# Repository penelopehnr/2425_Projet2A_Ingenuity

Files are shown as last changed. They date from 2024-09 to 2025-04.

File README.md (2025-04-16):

# 2425_Projet2A_Ingenuity

**Students :**

- Pénélope HENNER - penelope.henner@ensea.fr
- Kavin DUGARD - kevin.dugard@ensea.fr 
- Elio FLANDIN - elio.flandin@ensea.fr
- Joel COLASO - joel.colaso@ensea.fr

## Project background:

Mars 2020 is a space mission to deploy the Perseverance rover on the Martian surface to study its surface and collect soil samples. It is the first of a series of three missions whose ultimate aim is to return these samples to Earth for analysis.

Ingenuity is a small helicopter developed by NASA, the US space agency. It is being used experimentally on the surface of Mars during the Mars 2020 mission. The helicopter is on board the Perseverance rover.

On April 19, 2021, for the first time in the history of the space age, a spacecraft makes a powered flight through the tenuous atmosphere of another planet. Ingenuity's objective is optical reconnaissance of the terrain, with the helicopter taking numerous aerial photos used by the pilots of the Perseverance astromobile to identify obstacles and promising sites (taking rock samples from the Martian soil).

Ingenuity is a 1.8 kg helicopter with 2 coaxial counter-rotating rotors. It draws its energy from 6 lithium-ion batteries recharged by solar cells. Its navigation system enables it to follow a pre-programmed route without human intervention. Its only payload is a camera.

The mission recently came to an end (January 18, 2024) when a blade broke during the 72nd flight.

Ingenuity has opened up new prospects for Mars exploration. NASA and ESA, as part of their Mars sample return mission, are now including 2 similar helicopters to collect the tubes containing the Martian samples deposited by the Perseverance astromobile in the event of its failure.

 Our project is therefore to try to build the Ingenuity module in miniature. In other words, we want to create a vehicle that can move through the air and take a photo of what's going on below.

 [Learn more about the Mars 2020 mission](Ingenuity%20March%202020.md)

Ingenuity picture

## Our project

Our project is to try and make this helicopter in miniature mode. In other words, we want to create a vehicle that can move through the air and take a photo of what's happening below. To do this, we'll have a total of 10 sessions in which we'll have to mix PCBs, coding, soldering and so on.

## Project architecture

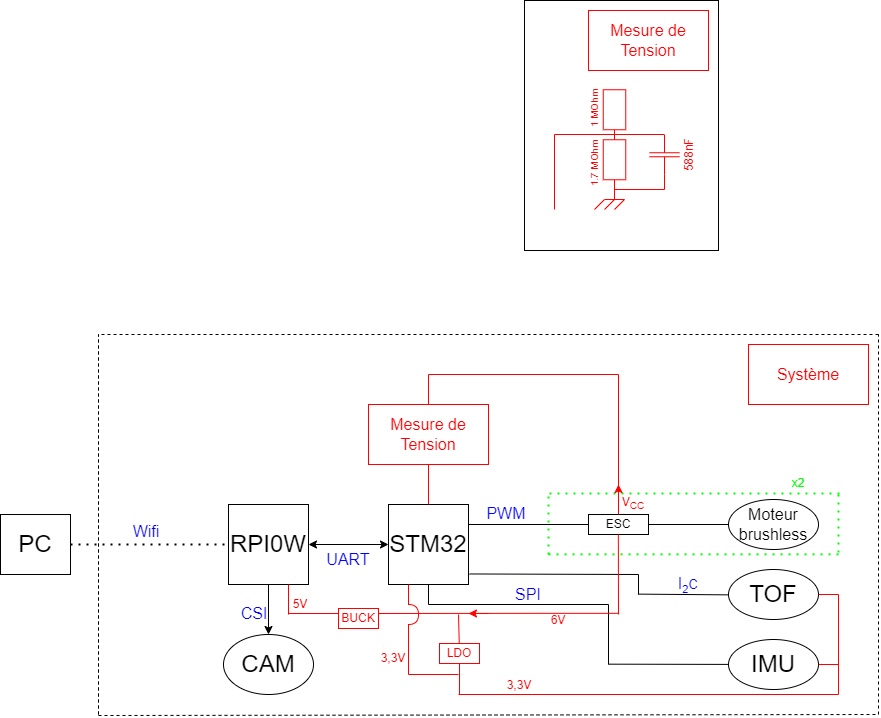
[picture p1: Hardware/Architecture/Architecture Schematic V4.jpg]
Mini Ingenuity Drone architecture


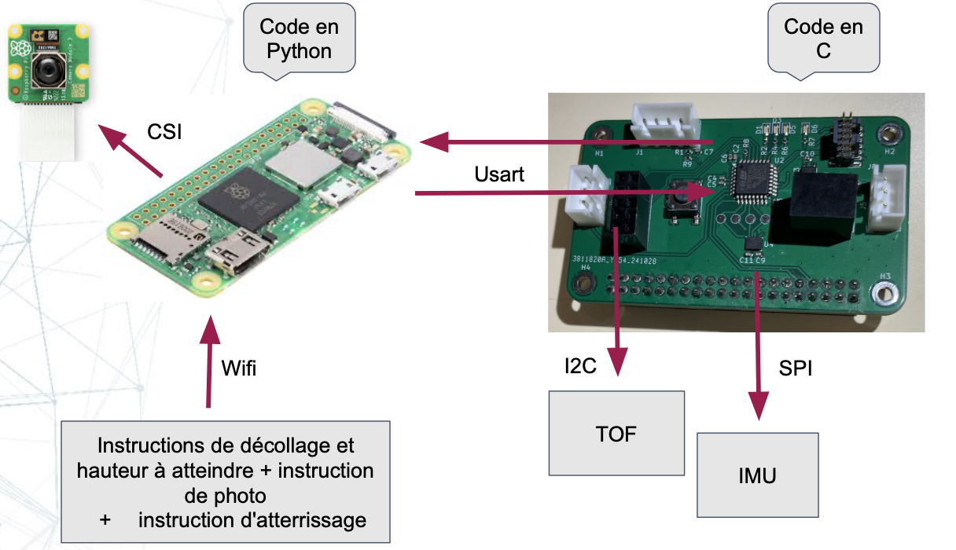
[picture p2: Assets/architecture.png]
Architecture explanations


## Description of repo structure:

``````
.
├── Assets/            # Project images (drone, PCB)
├── Datasheets/        # Component datasheets
├── Hardware/          # Architecture diagrams, KiCad (PCB) files and 3D files
├── Software/          # Embedded code (STM32) + Python code + TOF module
├── README.md          # Main project documentation
├── Ingenuity March 2020.md  # Background on the Mars 2020 mission

``````

In the **Assets** folder, you will find pictures of the drone and the assembled PCB.

The **Datasheets** folder contains documentation for all the components we used throughout the project.

The **Hardware** folder includes all the KiCad files needed to reproduce our custom PCB, along with the Bill of Materials (BOM) listing all components, their references, and specifications. You will also find files for 3D printing and laser cutting the various structural parts of the drone.

The **Software** folder contains:
- The **Python code** used to build the graphical user interface (GUI) on the PC to communicate with the Raspberry Pi (`Client_GUI.py`).
- The **Python code** running on the Raspberry Pi, which handles communication with the microcontroller and takes pictures (`server.py`).
- The **TOF code** (developed with STM32CubeIDE), which is responsible for sending the drone’s altitude using a Time-of-Flight sensor.
- The **C code** (also under STM32CubeIDE) in `Ingenuity_2A`, running on the STM32 microcontroller, which receives commands from the Raspberry Pi and manages the components such as motors, TOF sensor, etc.

## Environments used: 

### Machines Used
- **PC (Windows/macOS/Linux)**: Used for development (STM32CubeIDE, Python, OnShape, etc.).
- **Function Generator (GBF)**: Used to simulate control signals during motor testing.
- **Laser Cutter (FabLab)**: Used to cut the wooden drone structure.

### Hardware
- **Raspberry Pi Zero**: A single-board computer used for image capture, PCB interfacing, and running Python scripts.
- **STM32L412KBT6**: Main microcontroller used on the custom PCB.
- **VL53L1X**: Time-of-Flight (ToF) distance sensor.
- **ESC (Electronic Speed Controllers)**: To control brushless motors.
- **Brushless Motors**: Used to generate drone thrust.
- **LDO BU33TD3WG**: Low-dropout voltage regulator.
- **Buck Converter 17395xx36**: DC-DC converter used to step down voltage.
- **MOSFETs**: Used for power switching and motor control.
- **Camera (connected to Raspberry Pi)**: Captures aerial images.

### Software
#### Embedded Development
- **STM32CubeIDE**: Used to write, compile, and flash firmware to the microcontroller.
- **STM32 HAL Drivers**: Low-level drivers for managing STM32 peripherals.

#### Electronic Design
- **KiCad**: Used for circuit schematic design, PCB layout, and Gerber/BOM export.
- **OnShape**: Used for 3D modeling of the drone structure.

#### Python Development
- **Python 3**: Used for drone communication scripts and the graphical user interface (GUI).
- **Tkinter / PyQt**: Used to build the GUI interface.
- **Pygame / Other sound libraries**: For playing feedback sounds (from the `sounds/` folder).
- **Flask / TCP Sockets**: For communication between the GUI and the drone.

## Precision on the TOF VL53L1X

Start by copying the ```VL53L1X_ULD_API``` in your project. You want to configure the paths in your IDE (eg. in STM32CubeIDE : ```Project > Properties``` then ```C/C++ General > Paths and Symbols```).

Source (code and explanations): https://github.com/lfiack/tof_VL53L1X-SATEL/blob/main/README.md

## Precise notice of our project 

[Mini-Ingenuity notice](Mini-Ingenuity_notice.md)

## Logbook

[Logbook](LogBook.md)

## Picture of Mini-Ingenuity 

Picture of Mini-Ingenuity

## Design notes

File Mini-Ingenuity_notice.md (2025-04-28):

# Utilisation Notice

## General 

The goal of the drone is to take off, reach a predefined altitude, capture a photo, and then descend.

Altitude commands are sent from the PC to the Raspberry Pi Zero via Wi-Fi using Python scripts. A custom graphical interface has been developed on the PC to control this process. The Raspberry Pi then communicates with the microcontroller on the PCB through a UART (USART) serial connection, using both Python and C code. It is also responsible for capturing images through a CSI camera interface.

The microcontroller, embedded on the custom PCB, manages the drone's motors using PWM signals (written in C), and receives altitude data from a Time-of-Flight (TOF) sensor over an I2C bus, also handled via C code.

## Architecture 

Mini Ingenuity Drone architecture

## Structure of Mini-Ingenuity (Hardware files)

### 3D structural parts 
 
files concerned: `Hardware/3D files/files.stl`:
``````
3D files
│   │   ├── 3D_boulons_structure_drone.stl
│   │   ├── 3D_tube_structure_drone.stl
│   │   └── 3D_vises_structure_drone.stl
``````
The screws, bolts, and tubes allow you to assemble the wooden parts together and build the structure of the drone.

Machine used: a 3D printer

3D parts

### Wood structure 

files concerned: `Hardware/Wood structure/Bois.stl`

Our wood sheets are 5 mm thick. 

Machine used: a laser cutter 

### Picture of the Structure 

Picture of the structure

## PCB (Hardware files)

files concerned: `Hardware/KiCAD/...`

### BOM

First, you will need all the required components. You can find all the necessary information — references, quantities, etc. — in the Bill of Materials (BOM).

[BOM](Hardware/KiCAD/BOMv3.csv)

### KiCad

Software used: KiCad
All the KiCad files required to build the PCB are available in this repository.

Picture of the PCB: [PCB Picture](Assets/IMG_6468.png)

## Code (Software)

### Python code 

files concerned: `Software/Python`
requiered functions: `Software/Python/requirements.txt`
Notice : `Software/Python/Notice.md`

#### Initialization

Start by importing all the libraries listed in the `requirements` file. Follow the steps indicated in `Software/Python/Notice.md`.

#### Graphic User Interface

There are a total of five different buttons:  
- First, you must click on the gear icon in the top left corner. This allows you to enter your system's "coordinates": **IP** and **port**.  

- Then, press the button with the Wi-Fi logo on the right to connect to the RPi0 (Note that the script `Software/Python/server.py` must have been executed on the Raspberry Pi beforehand).  

- Now, let's go over the three remaining buttons:  
    - The button on the far left (***Command***) allows you to control the drone's altitude using your keyboard. Here are the available commands:  
        - Alt + UP_Arrow → +1   //   Alt + DOWN_Arrow → -1  
        - UP_Arrow → +5   //   DOWN_Arrow → -5  
        - Ctrl + UP_Arrow → +10   //   Ctrl + DOWN_Arrow → -10  
    - The center button (***Photo***) allows you to take a photo (how to retrieve it is explained in `Notice.md`).  
    - The button on the right (***Auto***) allows you to enter a specific height (in mm) for the drone to reach.

#### Emergency stop

If you want to do an Emergency stop, you just have to tap the ***esc*** touch on your keyboard, this will disconnect the computer to the RPi0 and the speed of the motor will decrease to zero. 

#### Get the photo

To get the photo, everything is explained in the `Software/Python/Notice.md` file. 

### Code for the microcontroller (STM32CubeIDE)

First, if you don't already have it, download the software STM32CubeIDE. 

Use the official ST website: https://www.st.com/en/development-tools/stm32cubeide.html

STM32CubeIDE download capture

Then also download our STM32 project ("Software/C" folder) from this github repository.

You can dowload the repository as shown in the following capture:



Now, you're ready to open the code with STM32CubeIDE. You can click "Open Project from File System..." and select the one you just downloaded.



After that, use the "Project Explorer" view to navigate to the "main.c" file as shown here:



Then plug your STLINK-V3SET cable into the PCB (Green circle in the picture):

STLINK Connected image

Plug the other end to the computer that's running STM32CubeIDE using an USB cable and you are ready to go.

Finally, click the "Run" button to load the program to the microcontroller and start it's execution.

Run program capture

The drone is now ready and will be waiting for the instructions sent by the python powered user interface.

files concerned: `Software/C`

#### PINs

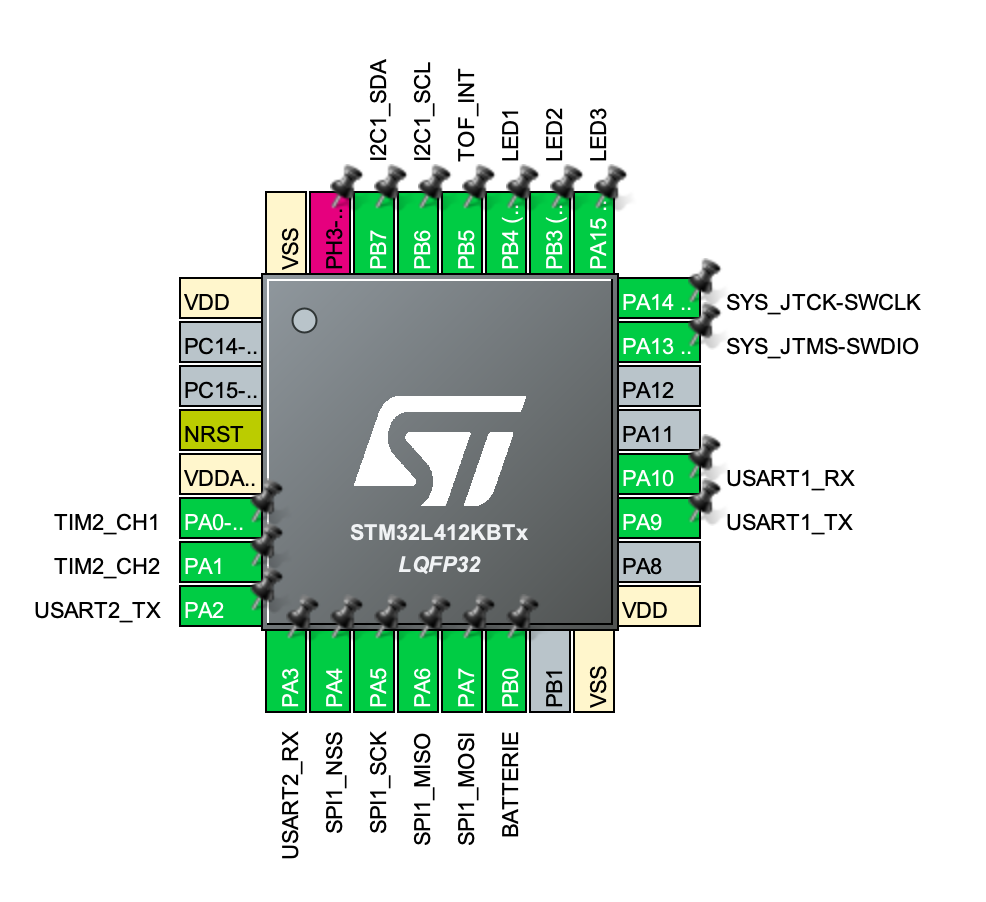
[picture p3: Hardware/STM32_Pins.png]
PIN


### TOF 

Start by copying the ```VL53L1X_ULD_API``` in your project. You want to configure the paths in your IDE (eg. in STM32CubeIDE : ```Project > Properties``` then ```C/C++ General > Paths and Symbols```).

detailed explanations: https://github.com/lfiack/tof_VL53L1X-SATEL/blob/main/README.md

You can refer to the datasheet for information on how to connect to the PCB: 

[TOF Datasheet](Datasheets/TOF.pdf)

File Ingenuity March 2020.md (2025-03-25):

# Ingenuity project 

## Introduction: Ingenuity as part of the Mars 2020 mission. 

Mars 2020 is a space mission that will deploy the Perseverance rover on the Martian surface to study its surface and collect soil samples. It is the first of a series of three missions whose ultimate aim is to return these samples to Earth for analysis. 

Ingenuity is a small helicopter developed by NASA, the US space agency. It is being used experimentally on the surface of Mars during the Mars 2020 mission.
The helicopter is on board the Perseverance rover. 

On April 19, 2021, for the first time in the history of the space age, a spacecraft makes a powered flight through the tenuous atmosphere of another planet. Ingenuity's objective is optical reconnaissance of the terrain, with the helicopter taking numerous aerial photos which are used by the pilots of the Perseverance astromobile to identify obstacles and promising sites (taking rock samples from the Martian soil). The tenuous atmosphere (only 1% of Earth's atmospheric pressure) offers very little lift, making it more difficult to develop an aerobot. 

Ingenuity is a 1.8 kg helicopter with 2 coaxial counter-rotating rotors. It draws its energy from 6 lithium-ion batteries recharged by solar cells. Its navigation system enables it to follow a pre-programmed route without human intervention. Its only payload is a camera. 

The mission recently came to an end (January 18, 2024) when a blade broke during the 72nd flight. 

Ingenuity has opened up new prospects for Mars exploration. NASA and ESA, in their Mars Sample Return mission, are now including 2 similar helicopters which will be responsible for collecting the tubes containing the Mars samples deposited by the Perseverance astromobile in the event of its failure. 

The Mars Sample Return mission will be Ingenuity's first operational use. Developed by NASA in collaboration with the European Space Agency, its aim is to return to Earth the Martian soil samples collected by the Perseverance astromobile. To achieve this objective, the mission plans to send a lander, Sample Retrieval Lander (SRL), carrying a remotely operated arm to retrieve the tubes containing the soil samples. If the soil samples are out of reach of the lander due to a failure of Perseverance, SRL has two Sample Recovery Helicopters, directly derived from the Ingenuity helicopter, equipped with a grabber to retrieve the tubes from where they were deposited.

## First look at the anatomy of the Martian helicopter

NASA's website with extensive information on Ingenuity: (https://mars.nasa.gov/technology/helicopter/#)

## Exploring helicopter operation

### Propulsion: 

The helicopter moves through the air thanks to two coaxial, two-bladed counter-rotating rotors. The rotational speed is between 2,400 and 2,900 rpm, ten times that of a helicopter main rotor on Earth, to be effective in the thin air of Mars. This is a condition we won't be able to meet. 

Understanding how helicopter propellers work helps us to overcome the first difficulties: we need small, coaxial, counter-rotating propellers, parts that we can't build ourselves (3D printing). One solution we've come up with is to use propellers taken from a remote-controlled helicopter. We'll dismantle the aircraft to keep only the propellers on the axis and the engines, and rebuild all the electronics according to our specifications. 

Aircraft type: the use of coaxial counter-rotating rotors saves space compared with the use of an anti-torque rotor. 

### Energy: 

Energy is the main limiting factor concerning the helicopter's capabilities. The energy required for propulsion, sensor operation (altimeter, camera), heating resistors (responsible for maintaining the various systems at a temperature compatible with the operating constraints during the Martian night), avionics, processors and the telecommunications system is supplied by six lithium-ion accumulators, with a capacity of 36 Watts-h recharged by photovoltaic cells (active surface area of 544 cm^2).

### Sensors: 

- a navigation camera
- 2 3-axis inertial units (acceleration and rotation speed)
- 2-axis inclinometer
- altimeter

### Telecommunications: 

Given the time taken for Mars-to-Earth communication (around ten minutes in favorable conditions), the helicopter flies autonomously, applying instructions transmitted beforehand. In flight, the helicopter does not receive, but transmits the data it has collected. 

### Avionics and processors:

The avionics are distributed over 5 circuit boards, 4 of which form the sides of the cubic fuselage and the fifth the inside. The on-board computer uses a Snapdragon microprocessor clocked at 2.26 GHz, with 2 GB RAM and 32 GB flash memory. The computer supports the navigation function and controls the rotors via two redundant microcontrollers. The software running on the microprocessor is supported by an FPGA-type integrated circuit, which handles functions such as altitiude control, I/O management of the inertial unit, altimeter and inclinometer, and telecommunications management. The FPGA is a militarized version of MicroSemi's ProASIC3L. The operating system is GNU/Linux. 

### Sources: 

https://mars.nasa.gov/technology/helicopter/#Tech-Specs

https://fr.wikipedia.org/wiki/Ingenuity_(hélicoptère)

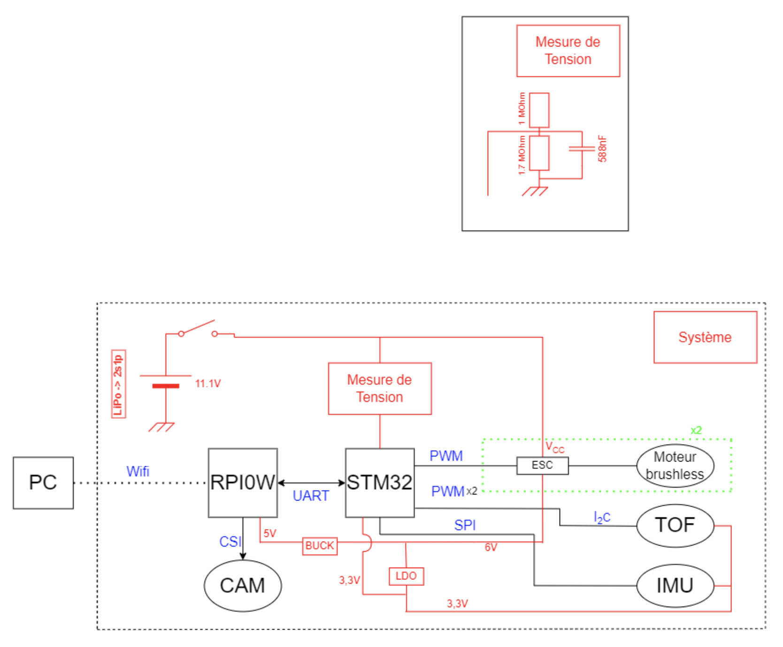
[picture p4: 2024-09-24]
Hardware/Architecture/Architecture Schematic V2.jpg

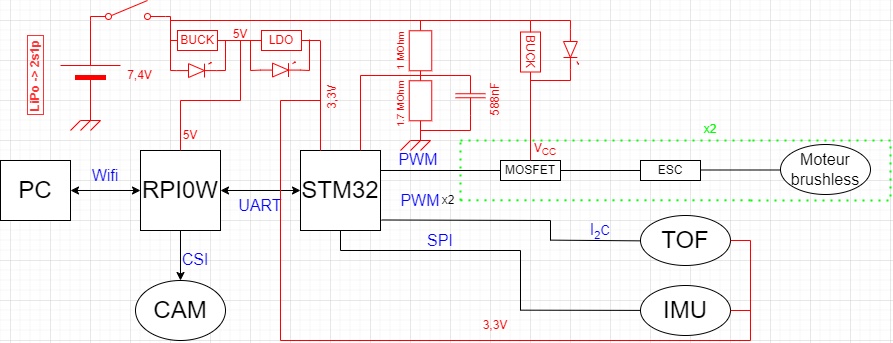
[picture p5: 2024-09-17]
Hardware/Architecture/Architecture Schematic V1.jpg

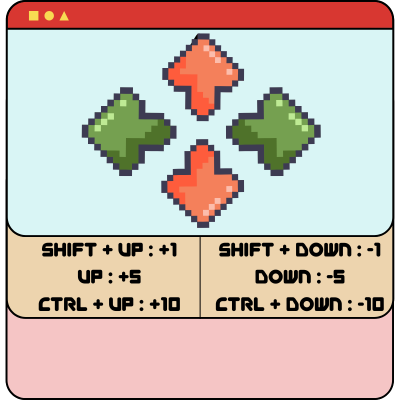
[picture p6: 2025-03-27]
Software/Python/img/Command.png

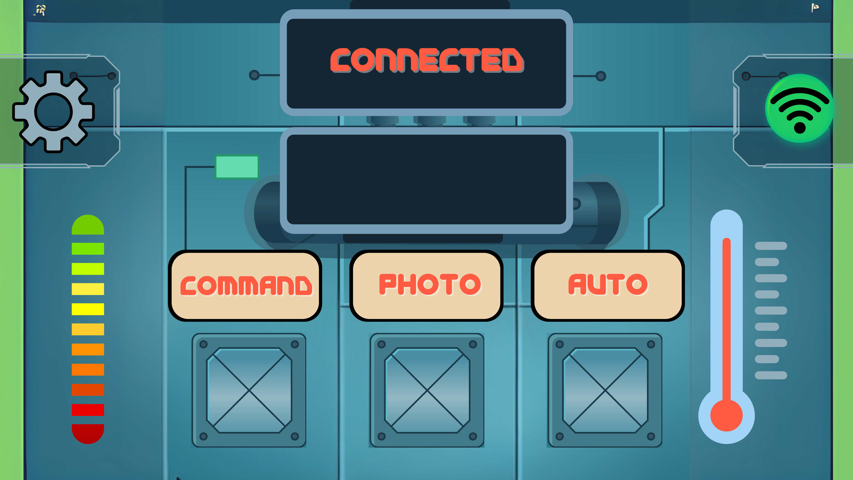
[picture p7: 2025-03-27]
Software/Python/img/Connected.png

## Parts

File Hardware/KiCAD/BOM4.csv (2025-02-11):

Reference | Value | Datasheet | Footprint | Qty | DNP | MPN
C1 | 10u | ~ | Capacitor_SMD:C_0603_1608Metric | 1
C2,C3,C4,C5,C7,C9,C11 | 100n | ~ | Capacitor_SMD:C_0402_1005Metric | 7
C6 | 4u7 | ~ | Capacitor_SMD:C_0402_1005Metric | 1
C8,C10 | 1u | ~ | Capacitor_SMD:C_0402_1005Metric | 2
D1,D3,D5,D6 | LED | ~ | LED_SMD:LED_0603_1608Metric | 4
H1,H2,H3,H4 | MountingHole_Pad | ~ | MountingHole:MountingHole_2.7mm_M2.5_DIN965_Pad | 4
J1 | Conn_01x04 | ~ | Connector_JST:JST_XH_B4B-XH-A_1x04_P2.50mm_Vertical | 1
J2,J6 | Conn_02x05_Odd_Even | ~ | Connector_PinHeader_2.54mm:PinHeader_2x05_P2.54mm_Vertical | 2
J4,J5 | Conn_01x03 | ~ | Connector_JST:JST_XH_B3B-XH-A_1x03_P2.50mm_Vertical | 2
J8 | Conn_ST_STDC14 | https://www.st.com/content/ccc/resource/technical/document/user_manual/group1/99/49/91/b6/b2/3a/46/e5/DM00526767/files/DM00526767.pdf/jcr:content/translations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 | Connector_PinHeader_1.27mm:PinHeader_2x07_P1.27mm_Vertical_SMD | 1
R1 | 27k | ~ | Resistor_SMD:R_0402_1005Metric | 1
R2,R4,R6,R7 | 165 | ~ | Resistor_SMD:R_0402_1005Metric | 4
R8,R9 | 10k | ~ | Resistor_SMD:R_0402_1005Metric | 2
SW2 | SW_Push | ~ | Button_Switch_SMD:SW_Push_1P1T_NO_6x6mm_H9.5mm | 1
TP1 | TestPoint | ~ | TestPoint:TestPoint_Pad_D1.5mm | 1 | DNP
TP2,TP3,TP4,TP5,TP6 | TestPoint | ~ | TestPoint:TestPoint_Pad_D1.5mm | 5
U1 | ~ |  | myemp:Buck_ing | 1 |  | 173950536
U2 | STM32L412KBTx | https://www.st.com/resource/en/datasheet/stm32l412kb.pdf | Package_QFP:LQFP-32_7x7mm_P0.8mm | 1 |  | STM32L412KBT6
U3 | BU33TD3WG | https://ww1.microchip.com/downloads/aemDocuments/documents/OTH/ProductDocuments/DataSheets/MIC5317-High-Performance-Single-150mA-LDO-DS20006195B.pdf | Package_TO_SOT_SMD:SOT-23-5 | 1 |  | BU33TD3WG-TR
U4 | LSM6DSM | https://www.st.com/resource/en/datasheet/lsm6dsm.pdf | Package_LGA:LGA-14_3x2.5mm_P0.5mm_LayoutBorder3x4y | 1 |  | LSM6DSMTR

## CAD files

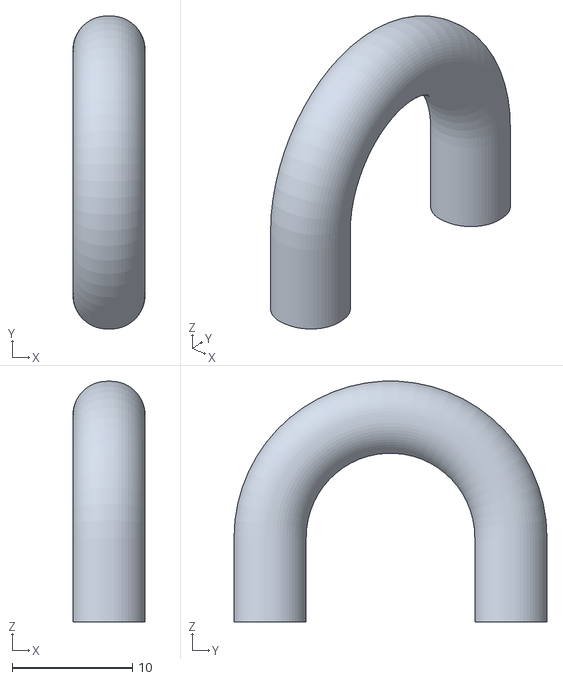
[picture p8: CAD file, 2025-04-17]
Hardware/3D files/3D_handle_structure_drone.stl
6.00 x 26.0 x 20.0

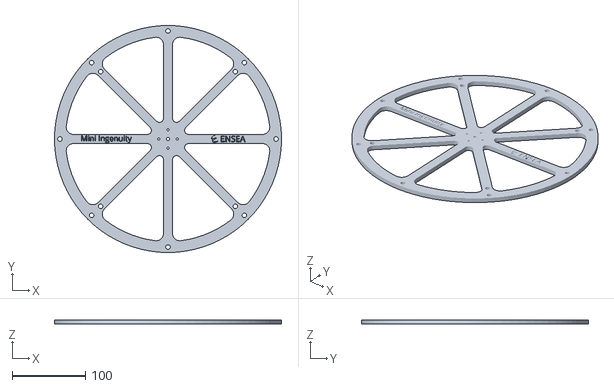
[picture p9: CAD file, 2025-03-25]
Hardware/Wood structure/Wooden_structure.stl
310.0 x 310.0 x 6.00

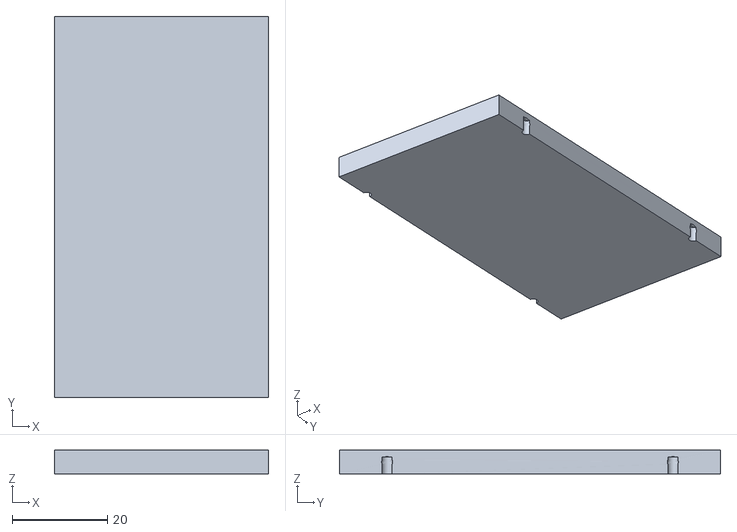
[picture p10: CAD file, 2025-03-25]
Hardware/3D files/3D_hatch_structure_drone.stl
45.0 x 80.0 x 5.00

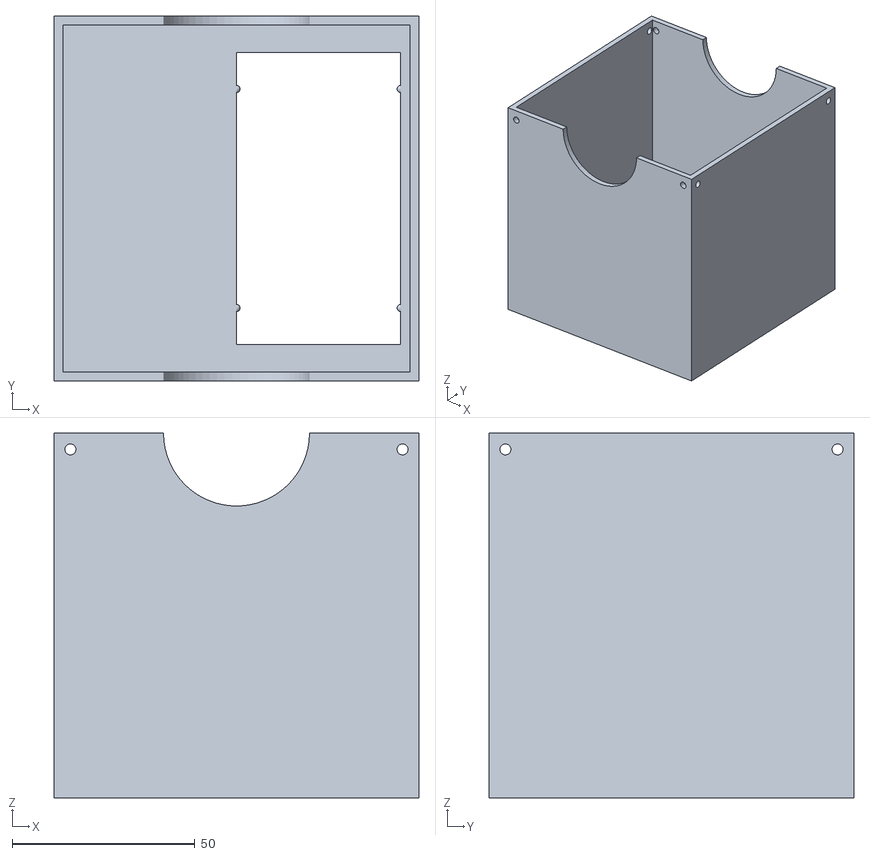
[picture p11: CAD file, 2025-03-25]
Hardware/3D files/3D_box_electronics_structure_drone.stl
100.0 x 100.0 x 100.0

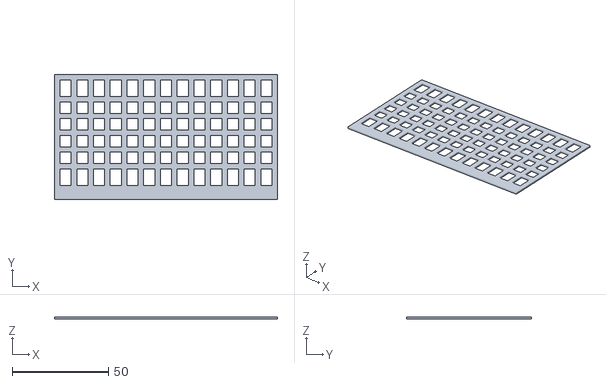
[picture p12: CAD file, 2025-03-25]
Hardware/3D files/3D_protection_structure_drone.stl
116.0 x 65.0 x 1.00

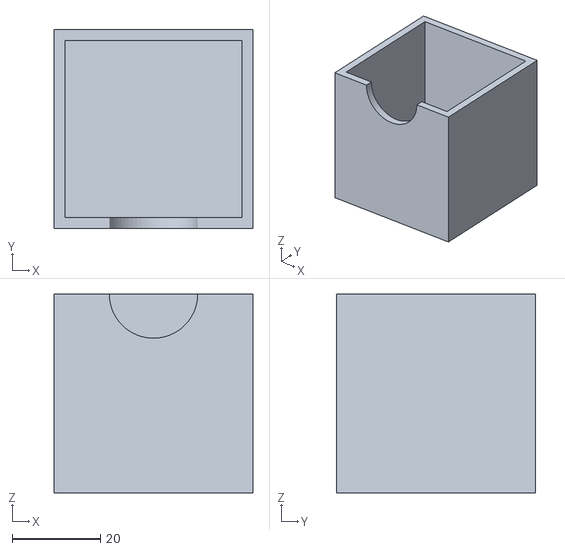
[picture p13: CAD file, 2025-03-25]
Hardware/3D files/3D_box_motor_structure_drone.stl
45.0 x 45.0 x 45.0

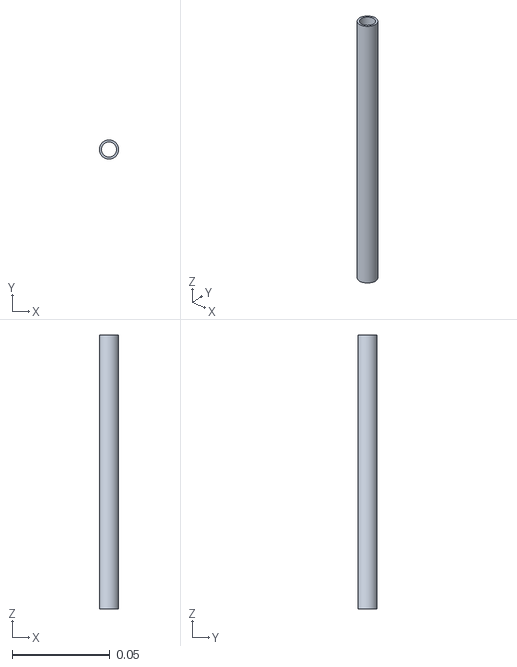
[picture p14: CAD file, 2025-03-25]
Hardware/3D files/3D_tube_structure_drone.stl
0.0098 x 0.0098 x 0.14

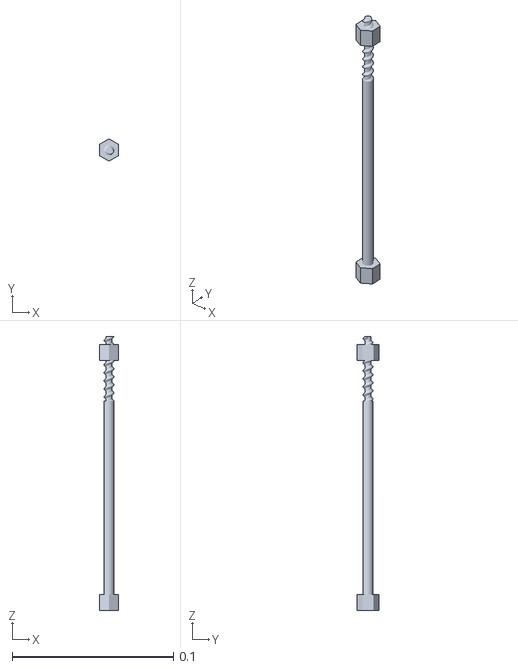
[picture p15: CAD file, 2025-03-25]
Hardware/3D files/3D_screw_structure_drone.stl
0.012 x 0.0139 x 0.17

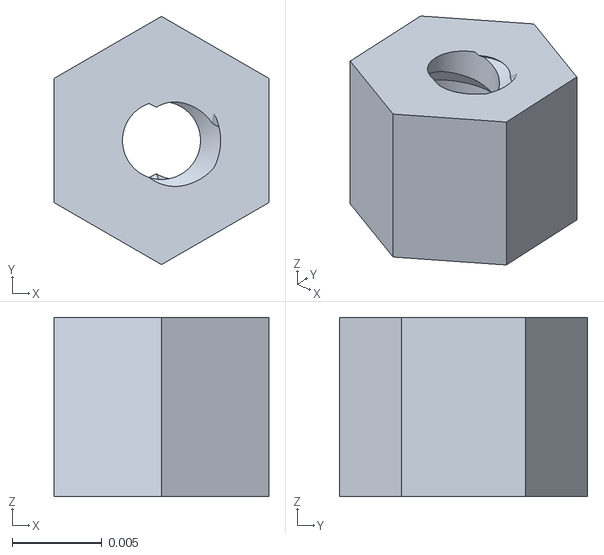
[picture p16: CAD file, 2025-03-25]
Hardware/3D files/3D_bolts_structure_drone.stl
0.012 x 0.0139 x 0.01

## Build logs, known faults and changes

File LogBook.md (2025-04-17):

## Project Logbook – Ingenuity

### Table of Contents
- [Session 1 (08/10/2024)](#session-1-08102024)
- [Session 2 (22/10/2024)](#session-2-22102024)
- [Session 3 (05/11/2024)](#session-3-05112024)
- [Session 4 (12/11/2024)](#session-4-12112024)
- [Session 5 (19/11/2024)](#session-5-19112024)
- [Session 6 (26/11/2024)](#session-6-26112024)
- [Session 7 (03/12/2024)](#session-7-03122024)
- [Session 8 (10/12/2024)](#session-8-10122024)
- [Session 9 (14/12/2024)](#session-9-14122024)
- [Session 10 (21/12/2024)](#session-10-21122024)
- [Session 11 (28/12/2024)](#session-11-28122024)
- [Session 12 (28/01/2025)](#session-12-28012025)
- [Session 13 (04/02/2025)](#session-13-04022025)
- [Session 14 (11/02/2025)](#session-14-11022025)
- [Session 15 (04/03/2025)](#session-15-04032025)
- [Session 16 (11/03/2025)](#session-16-11032025)
- [Session 17 (18/03/2025)](#session-17-18032025)
- [Session 18 (25/03/2025)](#session-18-25032025)
- [Session 19 (01/04/2025)](#session-19-01042025)

### Session 1 (08/10/2024)
- Modeled the initial architecture diagram (V1).
- Started writing the project structure.
- Researched higher-performing components compared to last year (Buck, LDO, motors, etc.).
- Added datasheets for the final selected components.

### Session 2 (22/10/2024)
- Reflected on the architecture and created versions V2 and V3.
- Added new component datasheets.

### Session 3 (05/11/2024)
- Uploaded the final datasheets to Git.
- Finalized architecture diagram (V4).
- Started schematic modeling in KiCad.
- Began C programming on the STM32.
- Started the Python code base.

### Session 4 (12/11/2024)
- Updated the Python code.
- Created documentation for the Python scripts.
- Continued PCB routing in KiCad.

### Session 5 (19/11/2024)
- Exported the Bill of Materials (BOM).
- Soldered the PCB at school.
- Completed PCB soldering between sessions 5 and 6.
- Translated the GitHub repository content into English.

### Session 6 (26/11/2024)
- Tested PCB functionality (LEDs lit up correctly).
- Updated and extended Python code.
- Desoldered the Buck converter due to incorrect output voltage (3V instead of 5V).
- Soldered a new Buck converter and updated the BOM.

### Session 7 (03/12/2024)
- Soldered a Y-cable to connect both ESC drivers simultaneously.
- Tested the drone using a Function Generator (GBF) only.
- Conducted a flight test using the functional PCB and GBF instead of a battery.
- Began 3D modeling the drone structure on OnShape.
- Continued development in both Python and C.

### Session 8 (10/12/2024)
- Visited the FabLab in Cergy to use the laser cutter for wooden drone parts.

### Session 9 (14/12/2024)
- Assembled the drone structure.
- Performed additional flight tests with the assembled drone, GBF, and PCB.
- Finalized the GitHub translation.
- Conducted multiple tests with the Raspberry Pi camera.

### Session 10 (21/12/2024)
- Fully revised and translated the README.
- Started development of a Python graphical interface.
- Soldered a JFT-to-banana cable to power the Raspberry Pi more efficiently and continued testing.

### Session 11 (28/12/2024)
- Finalized the Python GUI base.
- Modified KiCad due to a connection issue between the Raspberry Pi Zero and the PCB (reversed connector) → adjusted routing accordingly.
- Started development of TOF (Time-of-Flight) sensor code in C.

### Session 12 (28/01/2025)
- Final adjustments in KiCad: resized PCB to match the Raspberry Pi Zero form factor, completed routing, and prepared for manufacturing.
- Continued TOF sensor code development.

### Session 13 (04/02/2025)
- Drone testing: validated communication and functionality between the PCB, Raspberry Pi Zero, and ESCs using GBF signals. Fixed bugs.
- Improved motor control code in C: enabled gradual speed increases and added keyboard controls.
- Continued TOF code development.

### Session 14 (11/02/2025)
- Soldered the new version of the PCB.
- Tested communication with the Raspberry Pi Zero and improved the C code (added linear acceleration for motors).
- Enhanced the Python GUI: enabled full drone control (connection, camera, power).
- Considered the drone’s weight and explored optimization options.

### Session 15 (04/03/2025)
- Tested the new PCB: power supply and components functioned correctly.
- Added new features to the Python GUI.
- Continued development of C code (motor control + TOF data handling).

### Session 16 (11/03/2025)
- Finalized the TOF code and started IMU integration (C language).
- 3D modeling: designed motor protection casings and an enclosure for electronics.
- Created custom 3D screws and bolts to reduce weight vs traditional threaded rods.
- 3D printed all new parts.

### Session 17 (18/03/2025)
- Full drone test with TOF, IMU, and integrated C code for autonomous flight via GUI.
- Structural optimization: reduced wood frame thickness to cut weight.
- 3D printed updated structural parts.

### Session 18 (25/03/2025)
- 3D modeling: designed propeller protection grilles.
- 3D printed the new protective elements.
- Improved GitHub repository: reorganized and refined the ReadMe.

### Session 19 (01/04/2025)
- Finalized the GitHub repository: added pictures and reorganized the ReadMe and general documentation.
- Assembled the drone: mounted all electronic components onto the 3D-printed frame.
- Gave a flight demonstration of our drone in front of the professors.

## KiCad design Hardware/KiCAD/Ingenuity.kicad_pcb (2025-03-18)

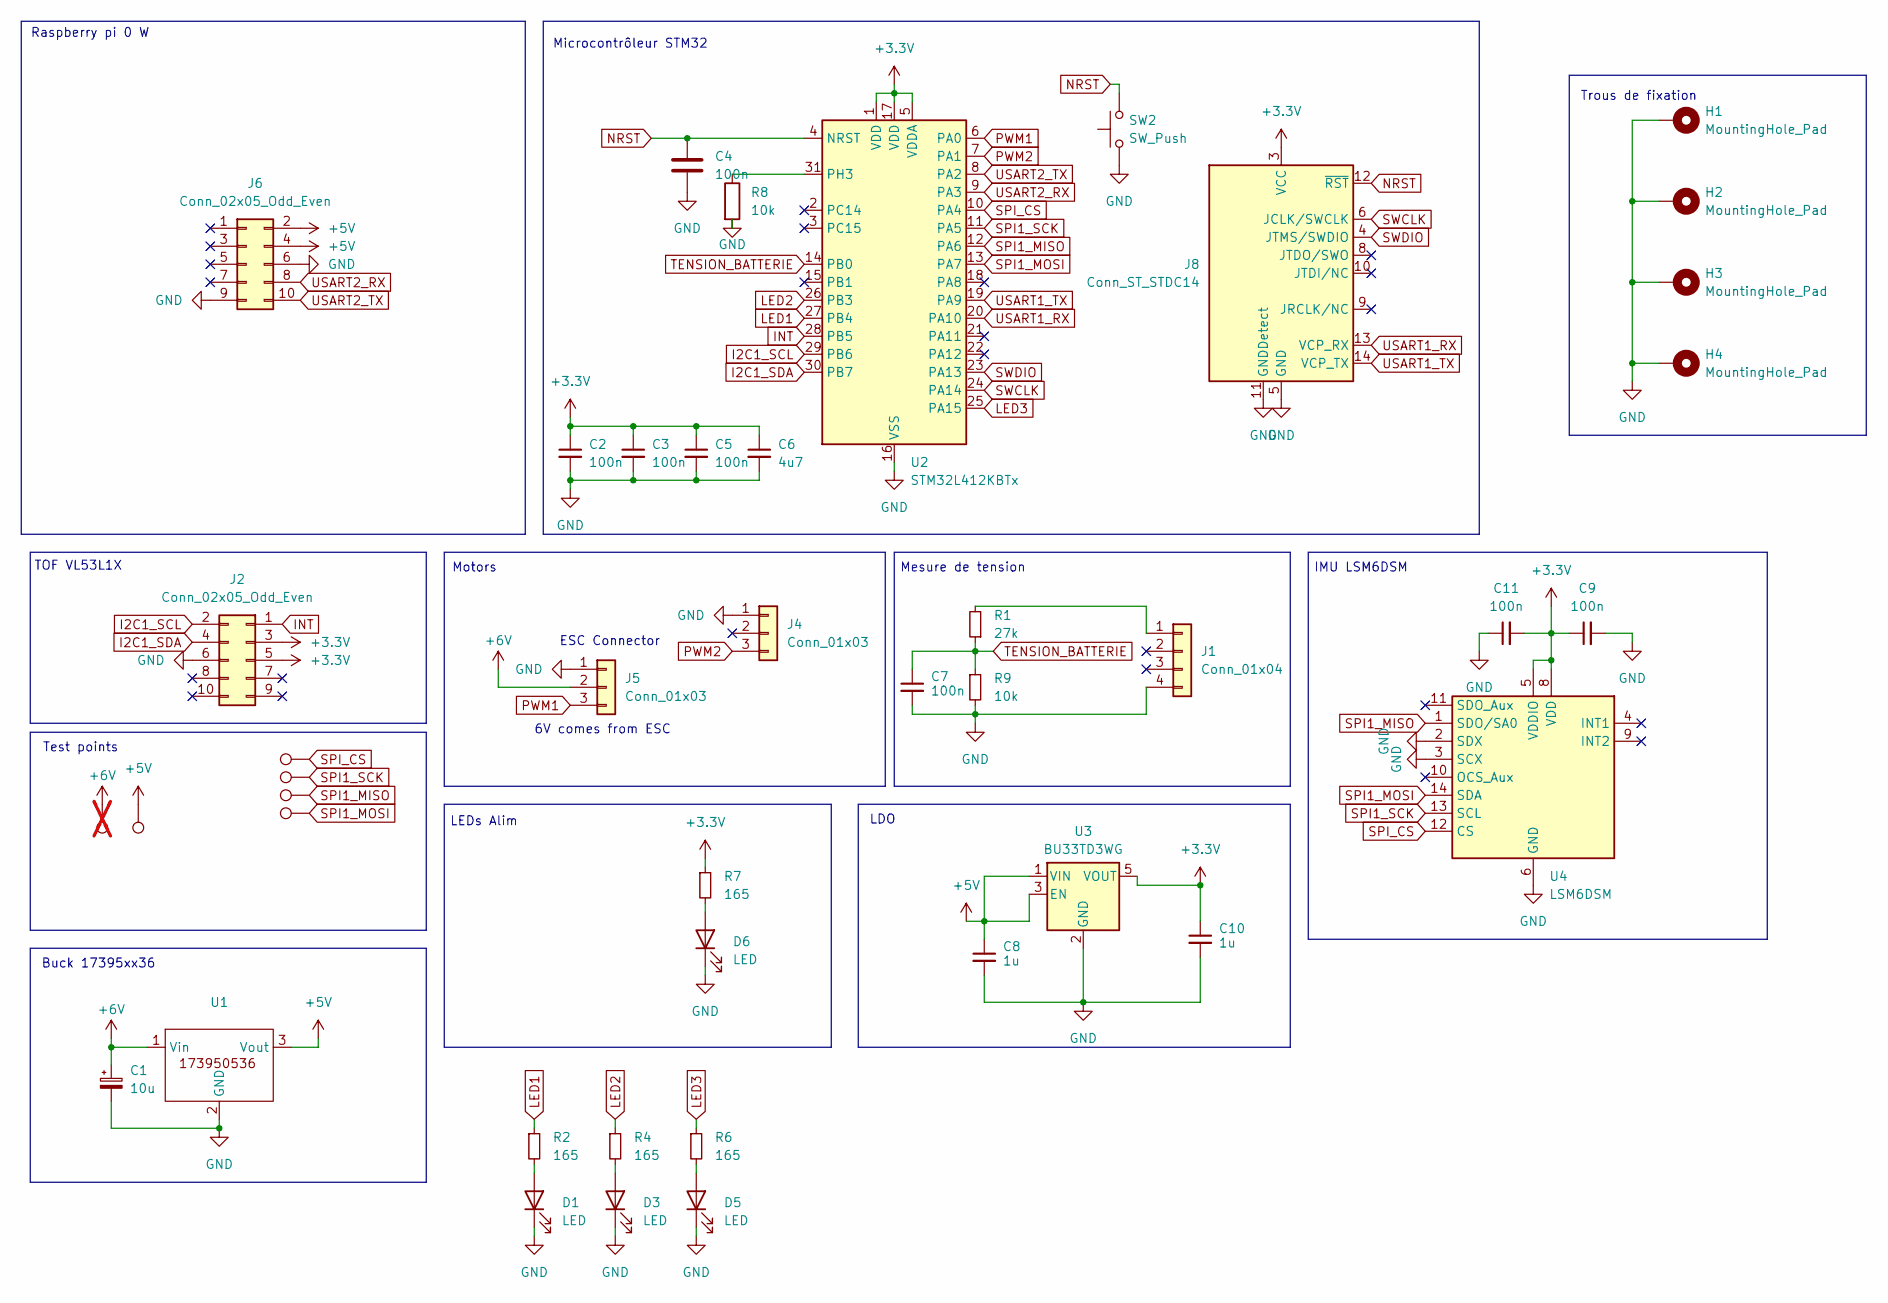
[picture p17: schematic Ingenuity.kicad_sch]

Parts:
C1: 10u; C_0603_1608Metric
C2, C3, C4, C5, C7, C9, C11: 100n; C_0402_1005Metric
C6: 4u7; C_0402_1005Metric
C8, C10: 1u; C_0402_1005Metric
D1, D3, D5, D6: LED; LED_0603_1608Metric
H1, H2, H3, H4: MountingHole_Pad; MountingHole_2.7mm_M2.5_DIN965_Pad
J1: Conn_01x04; JST_XH_B4B-XH-A_1x04_P2.50mm_Vertical
J2, J6: Conn_02x05_Odd_Even; PinHeader_2x05_P2.54mm_Vertical
J4, J5: Conn_01x03; JST_XH_B3B-XH-A_1x03_P2.50mm_Vertical
J8: Conn_ST_STDC14; PinHeader_2x07_P1.27mm_Vertical_SMD
R1: 27k; R_0402_1005Metric
R2, R4, R6, R7: 165; R_0402_1005Metric
R8, R9: 10k; R_0402_1005Metric
SW2: SW_Push; SW_Push_1P1T_NO_6x6mm_H9.5mm
TP1: TestPoint; TestPoint_Pad_D1.5mm; not fitted
TP2, TP3, TP4, TP5, TP6: TestPoint; TestPoint_Pad_D1.5mm
U1: Buck_ing; MPN 173950536
U2: STM32L412KBTx; LQFP-32_7x7mm_P0.8mm; MPN STM32L412KBT6
U3: BU33TD3WG; SOT-23-5; MPN BU33TD3WG-TR
U4: LSM6DSM; LGA-14_3x2.5mm_P0.5mm_LayoutBorder3x4y; MPN LSM6DSMTR

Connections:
+3.3V: C2.1, C3.1, C5.1, C6.1, C9.1, C10.1, C11.2, J2.3, J2.5, J8.3 (VCC), R7.1, U2.1 (VDD), U2.5 (VDDA), U2.17 (VDD), U3.5 (VOUT), U4.5 (VDDIO), U4.8 (VDD)
+5V: C8.1, J6.1, J6.2, J6.4, TP2.1, U1.3 (Vout), U3.1 (VIN), U3.3 (EN)
+6V: C1.1, J5.2, TP1.1, U1.1 (Vin)
GND: C1.2, C2.2, C3.2, C4.2, C5.2, C6.2, C7.2, C8.2, C9.2, C10.2, C11.1, D1.1 (K), D3.1 (K), D5.1 (K), D6.1 (K), H1.1, H2.1, H3.1, H4.1, J1.4, J2.6, J4.1, J5.1, J6.6, J6.9, J8.5 (GND), J8.7 (GND), J8.11 (GNDDetect), R8.2, R9.2, SW2.1, U1.2 (GND), U2.16 (VSS), U2.32 (VSS), U3.2 (GND), U4.2 (SDX), U4.3 (SCX), U4.6 (GND), U4.7 (GND)
I2C1_SCL: J2.2, U2.29 (PB6)
I2C1_SDA: J2.4, U2.30 (PB7)
INT: J2.1, U2.28 (PB5)
LED1: R2.1, U2.27 (PB4)
LED2: R4.1, U2.26 (PB3)
LED3: R6.1, U2.25 (PA15)
NRST: C4.1, J8.12 (~RST), SW2.2, U2.4 (NRST)
unnamed: D1.2 (A), R2.2
unnamed: D3.2 (A), R4.2
unnamed: D5.2 (A), R6.2
unnamed: D6.2 (A), R7.2
unnamed: J1.1, R1.2
unnamed: R8.1, U2.31 (PH3)
PWM1: J5.3, U2.6 (PA0)
PWM2: J4.3, U2.7 (PA1)
SPI1_MISO: TP5.1, U2.12 (PA6), U4.1 (SDO/SA0)
SPI1_MOSI: TP6.1, U2.13 (PA7), U4.14 (SDA)
SPI1_SCK: TP4.1, U2.11 (PA5), U4.13 (SCL)
SPI_CS: TP3.1, U2.10 (PA4), U4.12 (CS)
SWCLK: J8.6 (JCLK/SWCLK), U2.24 (PA14)
SWDIO: J8.4 (JTMS/SWDIO), U2.23 (PA13)
TENSION_BATTERIE: C7.1, R1.1, R9.1, U2.14 (PB0)
USART1_RX: J8.13 (VCP_RX), U2.20 (PA10)
USART1_TX: J8.14 (VCP_TX), U2.19 (PA9)
USART2_RX: J6.8, U2.9 (PA3)
USART2_TX: J6.10, U2.8 (PA2)

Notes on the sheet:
Trous de fixation
Mesure de tension
Motors
LDO
6V comes from ESC
Buck 17395xx36
Raspberry pi 0 W
IMU LSM6DSM
Test points
ESC Connector
LEDs Alim
Microcontrôleur STM32
TOF VL53L1X

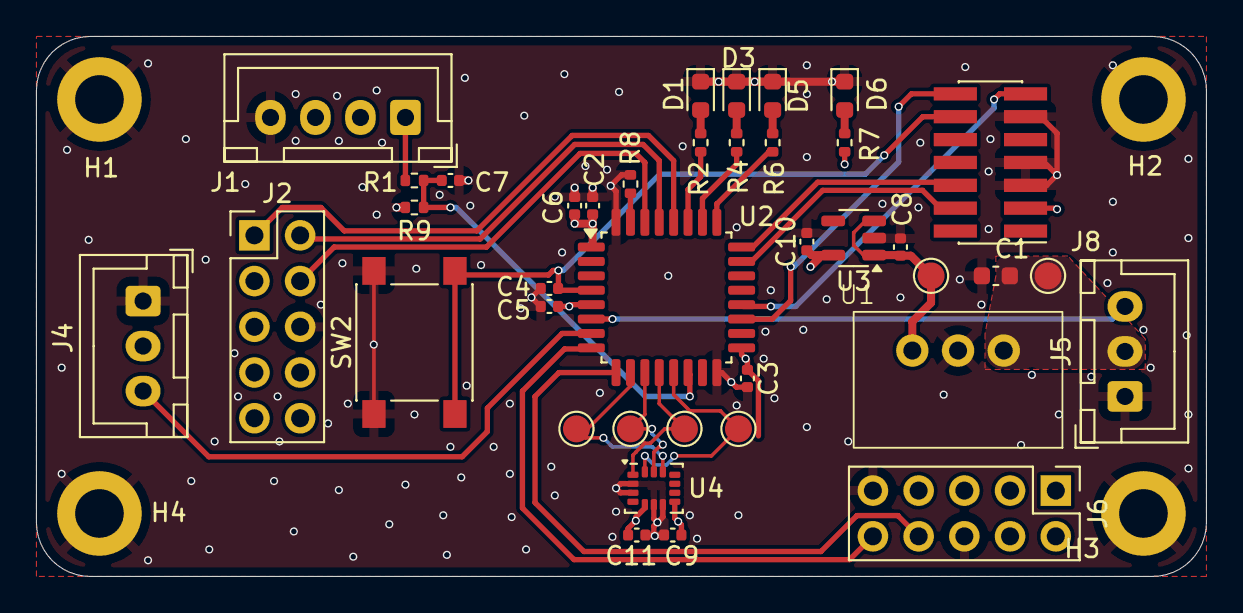
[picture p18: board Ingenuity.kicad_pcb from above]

Board: 4 copper layers, 65.0 x 30.0 mm, 43 parts (0 on the bottom side), 30 nets.

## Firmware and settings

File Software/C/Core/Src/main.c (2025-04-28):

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
/* Includes ------------------------------------------------------------------*/
#include "main.h"
#include "adc.h"
#include "i2c.h"
#include "spi.h"
#include "tim.h"
#include "usart.h"
#include "gpio.h"

/* USER CODE BEGIN Includes */
#include "string.h"
#include "motor.h"
#include "decodeInstruction.h"
#include "stdio.h"
#include "stdlib.h"
#include "math.h"

//////////////////////////////////////////////////////////////////////////////////////////////////////////////////
#include "VL53L1X_api.h"
#include "vl53l1_error_codes.h"


/* USER CODE END Includes */

/* USER CODE BEGIN PD */
#define MAX_ACK_MESSAGE_LENGTH 256

/////////////////////////////////////////////////////////////////////////////////////////////////////////////////
#define VL53L1X_DEFAULT_ADDRESS (0x29 << 1)

/* USER CODE END PD */


void SystemClock_Config(void);
/* USER CODE BEGIN 0 */
int __io_putchar(int ch)
{
  HAL_UART_Transmit(&huart1, (uint8_t *)&ch, 1, HAL_MAX_DELAY);
  return ch;
}

int __io_getchar(void)
{
  uint8_t ch = 0;
  __HAL_UART_CLEAR_OREFLAG(&huart1);
  HAL_UART_Receive(&huart1, (uint8_t *)&ch, 1, HAL_MAX_DELAY);
  HAL_UART_Transmit(&huart1, (uint8_t *)&ch, 1, HAL_MAX_DELAY);
  return ch;
}


char startChar = '@';
char endChar = '#';

uint8_t rx_char; // Variable to store the received character

char instruction[200];
int indexInstruction = 0;

int UARTReceiverState = 0;

volatile int flagUART1 = 0;
volatile int flagTIM6 = 0;


void HAL_TIM_PeriodElapsedCallback(TIM_HandleTypeDef * htim) {
	if (htim -> Instance == TIM6) {
		flagTIM6 = 1;
	}
}


void HAL_UART_RxCpltCallback(UART_HandleTypeDef *huart) {

	instruction[indexInstruction] = rx_char;
	indexInstruction++;

	// Re-enable UART interrupt reception
	HAL_UART_Receive_IT(&huart2, &rx_char, 1);

	if (rx_char == '#')
	{
		instruction[indexInstruction] = 0; // 0 character for the printf
		indexInstruction = 0;
		flagUART1 = 1;
	}
}


uint32_t measure_counter = 0;
uint8_t data_available = 0;
uint16_t distance;

void HAL_GPIO_EXTI_Callback(uint16_t GPIO_Pin)
{
	if (TOF_INT_Pin == GPIO_Pin)
	{
		measure_counter++;
		data_available++;
	}
}


/* USER CODE END 0 */

/**
  * @brief  The application entry point.
  * @retval int
  */
int main(void)
{

  /* MCU Configuration--------------------------------------------------------*/

  /* Reset of all peripherals, Initializes the Flash interface and the Systick. */
  HAL_Init();

  /* Configure the system clock */
  SystemClock_Config();

  /* Initialize all configured peripherals */
  MX_GPIO_Init();
  MX_ADC1_Init();
  MX_I2C1_Init();
  MX_SPI1_Init();
  MX_TIM2_Init();
  MX_USART1_UART_Init();
  MX_USART2_UART_Init();
  MX_TIM6_Init();
  /* USER CODE BEGIN 2 */

  //////////////////////////////////////////////////////////////////////////////////////////////////////////////////////////////////
	printf("\r\n===== VL53L1X-SATEL =====\r\n");

	uint16_t id;
	if (VL53L1X_GetSensorId(VL53L1X_DEFAULT_ADDRESS, &id) != VL53L1_ERROR_NONE)
	{
		Error_Handler();
	}
	printf("SensorID : 0x%X\r\n", id);

	VL53L1X_Version_t version;
	if (VL53L1X_GetSWVersion(&version) != VL53L1_ERROR_NONE)
	{
		Error_Handler();
	}
	printf("Version : %u.%ub%ur%lu\r\n", version.major, version.minor, version.build, version.revision);

	uint8_t boot_state = 0;
	uint8_t boot_state_counter = 0;

	while(boot_state == 0)
	{
		boot_state_counter++;
		if (VL53L1X_BootState(VL53L1X_DEFAULT_ADDRESS, &boot_state) != VL53L1_ERROR_NONE)
		{
			Error_Handler();
		}
		HAL_Delay(1);
	}

	printf("Chip booted in %d...\r\n", boot_state_counter);

	//Loads the 135 bytes default values to initialize the sensor.
	if (VL53L1X_SensorInit(VL53L1X_DEFAULT_ADDRESS) != VL53L1_ERROR_NONE)
	{
		Error_Handler();
	}
	printf("Sensor initialized with the default values\r\n");

	if (VL53L1X_SetDistanceMode(VL53L1X_DEFAULT_ADDRESS, 1) != VL53L1_ERROR_NONE) // 1=short, limited to 1.3m
	{
		Error_Handler();
	}
	printf("Short distance mode\r\n");

	if (VL53L1X_SetTimingBudgetInMs(VL53L1X_DEFAULT_ADDRESS, 50) != VL53L1_ERROR_NONE) // in ms possible values [20, 50, 100, 200, 500]
	{
		Error_Handler();
	}

	if (VL53L1X_SetInterMeasurementInMs(VL53L1X_DEFAULT_ADDRESS, 50) != VL53L1_ERROR_NONE) // in ms, IM must be >= TB
	{
		Error_Handler();
	}

	printf("Timing budget set\r\n");

	if (VL53L1X_StartRanging(VL53L1X_DEFAULT_ADDRESS) != VL53L1_ERROR_NONE)
	{
		Error_Handler();
	}

	  ///////////////////////////////////////////////////////////////////////////////////////////////////////////////////////////////////





  //Start Timer 6
  HAL_TIM_Base_Start_IT(&htim6);

	printf("--------------EXECUTION BEGINS--------------\r\n\n");

	// We define the dictionary of variables that can get modified by receiving a UART signal
	float height = 0.0;
	float LEDState = 0.0;
	float eLanding = 0.0;
	char* variableNames[3] = {"height", "LEDState", "eLanding"};
	float* variablePointers[3] = {&height, &LEDState, &eLanding};
	DictOfFloatVariables dictOfVariables = {
		.n = 3,
		.variableNames = variableNames,
		.variables = variablePointers
	};


	h_motor_t upperMotor;
	h_motor_t lowerMotor;

	upperMotor.htim = &htim2;
	lowerMotor.htim = &htim2;

	upperMotor.channel = TIM_CHANNEL_1;
	lowerMotor.channel = TIM_CHANNEL_2;

	MOTOR_InitBoth(&lowerMotor, &upperMotor);


	// Important, initiate character reception.
	// This line also being in HAL_UART_RxCpltCallback's body ensures continuous reception
	HAL_UART_Receive_IT(&huart2, &rx_char, 1);



  /* USER CODE END 2 */

  /* Infinite loop */
  /* USER CODE BEGIN WHILE */

  // This variable sets if the vertical control is constant (0), proportional (1) or proportional-derivative (2)
  int approach = 1;

  // Variables for Proportional Derivative Approach
  float Kp = 1.0;
  float Kd = 0.5;

  float previousError = 0;
  float dt = 0.05; // Time step (I calculated it based on our tim6 configuration)

  while (1)
  {

	  if (data_available > 0)
		{
			data_available = 0;
			uint16_t newDistance;

			if (VL53L1X_ClearInterrupt(VL53L1X_DEFAULT_ADDRESS) != VL53L1_ERROR_NONE)
			{
				Error_Handler();
			}
			if (VL53L1X_GetDistance(VL53L1X_DEFAULT_ADDRESS, &newDistance) != VL53L1_ERROR_NONE)
			{
				Error_Handler();
			}

			if (height != 0 && newDistance == 0) {
				// keep current value of distance to make sure to avoid any division by zero
			} else {
				distance = newDistance;
			}
		}

	  if (flagTIM6 == 1) {
		  flagUART1 = 0;

		  //printf("distance(%lu) : %u\r\n", measure_counter, distance);

		  if (approach == 0) {
			  if(distance < height) {
				  int current_percentage = upperMotor.PercentageOfTotalPower;
				  MOTOR_SetPower(&upperMotor, current_percentage + 1);
				  MOTOR_SetPower(&lowerMotor, current_percentage + 1);
			  } else if(distance > height) {
				  int current_percentage = upperMotor.PercentageOfTotalPower;
				  MOTOR_SetPower(&upperMotor, current_percentage - 1);
				  MOTOR_SetPower(&lowerMotor, current_percentage - 1);
			  }
		  } else if (approach == 1) {
			  int maxPercentageVariation = 5;
			  if(distance < height) {
				  int distanceToGoal = height - distance;

				  int percentageVariation = distanceToGoal/10;

				  if (percentageVariation > maxPercentageVariation) {
					  percentageVariation = maxPercentageVariation;
				  }

				  int current_percentage = upperMotor.PercentageOfTotalPower;
				  MOTOR_SetPower(&upperMotor, current_percentage + percentageVariation);
				  MOTOR_SetPower(&lowerMotor, current_percentage + percentageVariation);

			  } else if(distance > height) {
				  int distanceToGoal = distance - height;

				  int percentageVariation = distanceToGoal/10;

				  if (percentageVariation > maxPercentageVariation) {
					  percentageVariation = maxPercentageVariation;
				  }

				  int current_percentage = upperMotor.PercentageOfTotalPower;
				  MOTOR_SetPower(&upperMotor, current_percentage - percentageVariation);
				  MOTOR_SetPower(&lowerMotor, current_percentage - percentageVariation);
			  }
		  } else if (approach == 2) {
			  int error = height - distance;

			  float P = Kp * error;

			  float derivative = (error - previousError) / dt;
			  float D = Kd * derivative;

			  float pdOutput = P + D;

			  int maxVariation = 5;
			  if (pdOutput > maxVariation) pdOutput = maxVariation;
			  if (pdOutput < -maxVariation) pdOutput = -maxVariation;

			  int currentPower = upperMotor.PercentageOfTotalPower;

			  MOTOR_SetPower(&upperMotor, currentPower + (int)pdOutput);
			  MOTOR_SetPower(&lowerMotor, currentPower + (int)pdOutput);

			  previousError = error;
		  }
	  }


	  // This is a test to check that instructions can correctly be received
	  // by UART and affect change (modified variables, LED toggled)
	  if (flagUART1 == 1) {
		  printf("instruction = %s\r\n", instruction);

		  flagUART1 = 0;

		  LabelValue lv = checkInstruction(instruction);
		  printLabelValue(lv);

		  if (isnan(lv.value)) {
			  // error case
		  } else {
			  int applyLVReturnValue = applyLabelValue(lv, dictOfVariables);

			  if (applyLVReturnValue) { // If the return value is 1, it failed
				  // error case
			  } else {
				  char ackReceivedSuccess[MAX_ACK_MESSAGE_LENGTH];

				  sprintf(ackReceivedSuccess, "Received %s", instruction);
				  HAL_UART_Transmit_IT(&huart2, (uint8_t*)ackReceivedSuccess, strlen(ackReceivedSuccess));
			  }
		  }


		  if (eLanding != 0.0) {
			  MOTOR_SetLinearBoth(&upperMotor, &lowerMotor, 0.0, 5000);
			  //wait 5 s
			  eLanding = 0.0;
		  } else {
			  // Old motor update based solely on height instruction, use if you don't want any control
			  //MOTOR_SetPower(&upperMotor, height);
			  //MOTOR_SetPower(&lowerMotor, height);
		  }


		  // You can use this LED test to check if communication works without any danger
		  if(LEDState != 0.0) {
			  HAL_GPIO_WritePin(GPIOA, GPIO_PIN_15, GPIO_PIN_SET);
		  } else {
			  HAL_GPIO_WritePin(GPIOA, GPIO_PIN_15, GPIO_PIN_RESET);
		  }
	  }
    /* USER CODE END WHILE */

    /* USER CODE BEGIN 3 */
  }
  /* USER CODE END 3 */
}

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


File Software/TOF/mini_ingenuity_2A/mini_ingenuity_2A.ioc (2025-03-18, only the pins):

Mcu.UserName=STM32L412KBTx
PA0-CK_IN.Signal=S_TIM2_CH1
PA1.Signal=S_TIM2_CH2
PA10.Signal=USART1_RX
PA2.Signal=USART2_TX
PA3.Signal=USART2_RX
PA4.Signal=SPI1_NSS
PA5.Signal=SPI1_SCK
PA6.Signal=SPI1_MISO
PA7.Signal=SPI1_MOSI
PA9.Signal=USART1_TX
PB0.GPIO_Label=BATTERIE
PB0.Signal=ADCx_IN15
PB5.GPIO_Label=TOF_INT
PB5.Signal=GPXTI5
PB6.Signal=I2C1_SCL
PB7.Signal=I2C1_SDA

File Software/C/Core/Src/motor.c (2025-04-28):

/*
 * motor.c
 *
 *  Created on: May 27, 2024
 *      Author: JoelC
 */


#include "motor.h"
#include "stdio.h"
#include "math.h"

// There are currently lots of prints in this file for testing
// Once the tests pass, they can be deleted

// assuming counter counts microseconds
// 20000 = 5% of 2ms
#define COUNTER_PERIOD 19999 //Maximal counter value
#define MIN_POWER_DUTY_CYCLE 6 //%
#define MAX_POWER_DUTY_CYCLE 10 //%


int percentageToMicrosecondsAtHighState(float percentage) {
	float neededDutyCycle = MIN_POWER_DUTY_CYCLE + (MAX_POWER_DUTY_CYCLE - MIN_POWER_DUTY_CYCLE) * 0.01 * percentage;
	printf("->      neededDutyCycle = %f percent \r\n", neededDutyCycle);

	return (int) (COUNTER_PERIOD + 1) * 0.01 * neededDutyCycle;
}


void MOTOR_SetPower(h_motor_t* h_motor, float percentage) {
	if (percentage > 100) {
		percentage = 100;
	}

	if (percentage < 0) {
		percentage = 0;
	}

	printf("-> power set to %f percent \r\n", percentage);

	int microsecondsAtHighState = percentageToMicrosecondsAtHighState(percentage);

	__HAL_TIM_SET_COMPARE(h_motor->htim, h_motor->channel, microsecondsAtHighState);

	printf("->      microsecondsAtHighState = %d \r\n", microsecondsAtHighState);

	h_motor -> PercentageOfTotalPower = percentage;
}

void MOTOR_SetBoth(h_motor_t* h_motor1, h_motor_t* h_motor2, float percentage) {
	if (percentage > 100) {
		percentage = 100;
	}

	if (percentage < 0) {
		percentage = 0;
	}

	printf("-> power set to %f percent \r\n", percentage);

	int microsecondsAtHighState = percentageToMicrosecondsAtHighState(percentage);

	__HAL_TIM_SET_COMPARE(h_motor1->htim, h_motor1->channel, microsecondsAtHighState);
	__HAL_TIM_SET_COMPARE(h_motor2->htim, h_motor2->channel, microsecondsAtHighState);

	printf("->      microsecondsAtHighState = %d \r\n", microsecondsAtHighState);

	h_motor1 -> PercentageOfTotalPower = percentage;
	h_motor2 -> PercentageOfTotalPower = percentage;
}



void MOTOR_Init(h_motor_t* h_motor) {
	printf("INITIALISATION STARTED\r\n");

	MOTOR_SetPower(h_motor, 100);

	HAL_TIM_PWM_Start(h_motor->htim, h_motor->channel);

	HAL_Delay(2000);

	MOTOR_SetPower(h_motor, 0);
	HAL_Delay(3000);

	printf("INITIALISATION COMPLETED\r\n");
}


void MOTOR_InitBoth(h_motor_t* h_motor1, h_motor_t* h_motor2) {
	printf("INITIALISATION STARTED\r\n");

	MOTOR_SetPower(h_motor1, 100);
	MOTOR_SetPower(h_motor2, 100);

	HAL_TIM_PWM_Start(h_motor1->htim, h_motor1->channel);
	HAL_TIM_PWM_Start(h_motor2->htim, h_motor2->channel);

	HAL_Delay(2000);

	MOTOR_SetPower(h_motor1, 0);
	MOTOR_SetPower(h_motor2, 0);
	HAL_Delay(3000);

	printf("INITIALISATION COMPLETED\r\n");
}


void MOTOR_TurnOff(h_motor_t* h_motor) {
	MOTOR_SetPower(h_motor, 0);
}


// This function is blocking so it is not recommended
void MOTOR_SetLinear(h_motor_t* h_motor, float finalPercentage, int timeInMilliseconds) {

	float initialPercentage = h_motor -> PercentageOfTotalPower;

	int millisInterval = 50;

	if (2*millisInterval > timeInMilliseconds) {
		millisInterval = 50;
		timeInMilliseconds = 4000;
	}

	int nSteps = timeInMilliseconds / millisInterval;

	float currentPercentage = initialPercentage;
	float percentagePerStep = (finalPercentage - initialPercentage) / nSteps;


	for (int i = 0; i < nSteps; i++) {
		currentPercentage += percentagePerStep;

		MOTOR_SetPower(h_motor, currentPercentage); // Needs SetPower to take float input
		HAL_Delay(millisInterval);
	}

}

void MOTOR_SetLinearBoth(h_motor_t* h_motor1, h_motor_t* h_motor2, float finalPercentage, int timeInMilliseconds) {
	//Assumes both motors are set to the same power value
	float initialPercentage = h_motor1 -> PercentageOfTotalPower;

	int millisInterval = 50;

	if (2*millisInterval > timeInMilliseconds) {
		millisInterval = 50;
		timeInMilliseconds = 4000;
	}

	int nSteps = timeInMilliseconds / millisInterval;

	float currentPercentage = initialPercentage;
	float percentagePerStep = (finalPercentage - initialPercentage) / nSteps;

	for (int i = 0; i < nSteps; i++) {
		currentPercentage += percentagePerStep;

		MOTOR_SetPower(h_motor1, currentPercentage);
		MOTOR_SetPower(h_motor2, currentPercentage);
		HAL_Delay(millisInterval);
	}

}

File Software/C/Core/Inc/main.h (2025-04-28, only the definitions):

#define BATTERIE_Pin GPIO_PIN_0
#define BATTERIE_GPIO_Port GPIOB
#define LED3_Pin GPIO_PIN_15
#define LED3_GPIO_Port GPIOA
#define LED2_Pin GPIO_PIN_3
#define LED2_GPIO_Port GPIOB
#define LED1_Pin GPIO_PIN_4
#define LED1_GPIO_Port GPIOB
#define TOF_INT_Pin GPIO_PIN_5
#define TOF_INT_GPIO_Port GPIOB
#define TOF_INT_EXTI_IRQn EXTI9_5_IRQn

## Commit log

2024-09-17 datasheet MOSFET
2024-09-24 datasheet added buck
2024-10-08 Project STM32
2024-10-08 changement kicad
    [Ingenuity.kicad_sch]
2024-11-12 maj BOM-MPN
    [BOMv2.csv, Ingenuity.kicad_sch]
2024-11-19 update MPN BOMv3
    [BOMv3.csv, Ingenuity.kicad_sch]
2024-12-10 pcb picture
2024-12-19 File name translated
    [Project Materials.xlsx]
2024-12-20 Updated code with main (containing 3 tests), motor.c, decodeInstruction.c, updated timer configuration PWM
2025-01-21 update RasPi connector
    [Ingenuity-B_Cu.gbr, Ingenuity-B_Mask.gbr, Ingenuity-B_Silkscreen.gbr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]
2025-01-28 Kicad update
2025-01-28 update kicad reduction taille pcb
    [Ingenuity.kicad_pcb, Ingenuity.kicad_sch]
2025-01-28 end kicad V2
    [Ingenuity.kicad_pcb]
2025-01-29 change pcb dimensions and fix errors, ready for fab
    [Ingenuity.kicad_pcb]
2025-02-04 KiCad PCB V2
2025-02-04 update KiCad
2025-02-11 update BOM
    [BOM4.csv, Ingenuity.csv]
2025-03-03 modif KiCad
2025-03-25 "d fils
    [3D_boulons_structure_drone.stl, 3D_tube_structure_drone.stl, 3D_vises_structure_drone.stl]
2025-03-25 add 3D design
    [3D_box_elec_structure_drone.stl, 3D_box_moteur_structure_drone.stl, 3D_hatch_structure_drone.stl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]
2025-03-25 wood structure
    [Bois.stl]
2025-03-27 Files name translated
    [3D_bolts_structure_drone.stl, Wooden_structure.stl]
2025-04-17 3D design added
    [3D_box_elec_structure_drone.stl, 3D_box_moteur_structure_drone.stl, 3D_handle_structure_drone.stl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]
2025-04-28 Updated STM32 code

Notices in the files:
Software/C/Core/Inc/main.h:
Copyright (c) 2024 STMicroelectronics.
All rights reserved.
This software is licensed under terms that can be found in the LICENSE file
